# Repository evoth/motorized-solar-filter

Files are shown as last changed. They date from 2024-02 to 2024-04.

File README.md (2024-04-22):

# Motorized Solar Filter

A 3D printed solar filter that uses an SG90 servo to remove the solar film from your camera during totality!

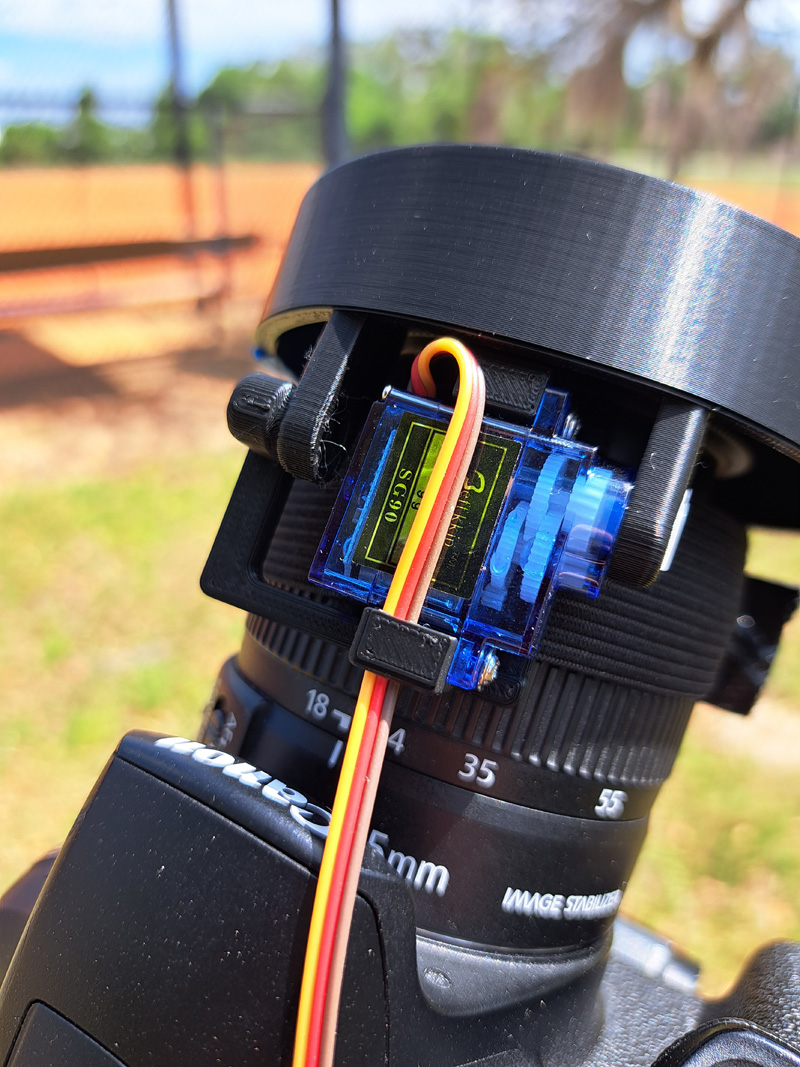
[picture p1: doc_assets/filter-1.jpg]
[](/doc_assets/filter-1_full.jpg)
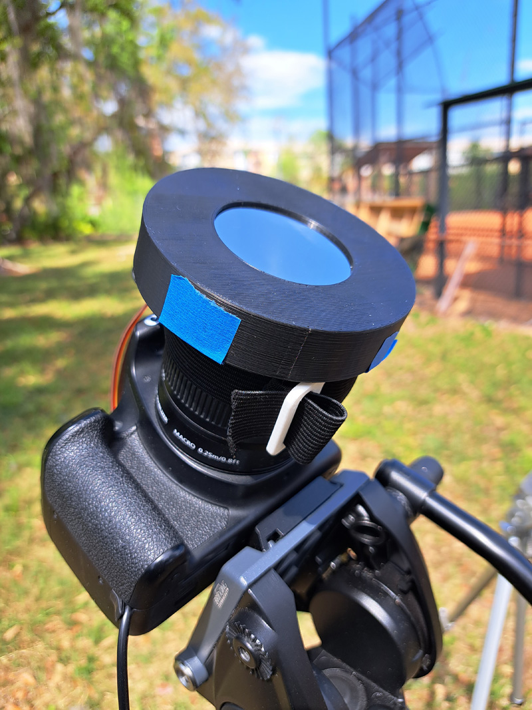
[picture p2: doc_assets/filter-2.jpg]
[](/doc_assets/filter-2_full.jpg)
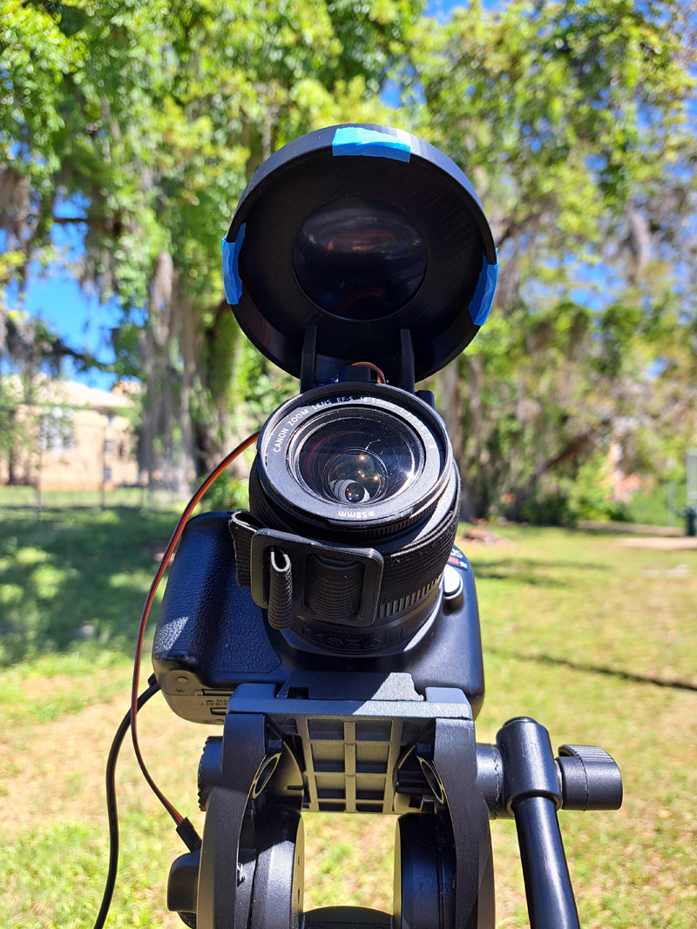
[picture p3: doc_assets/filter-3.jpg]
[](/doc_assets/filter-3_full.jpg)
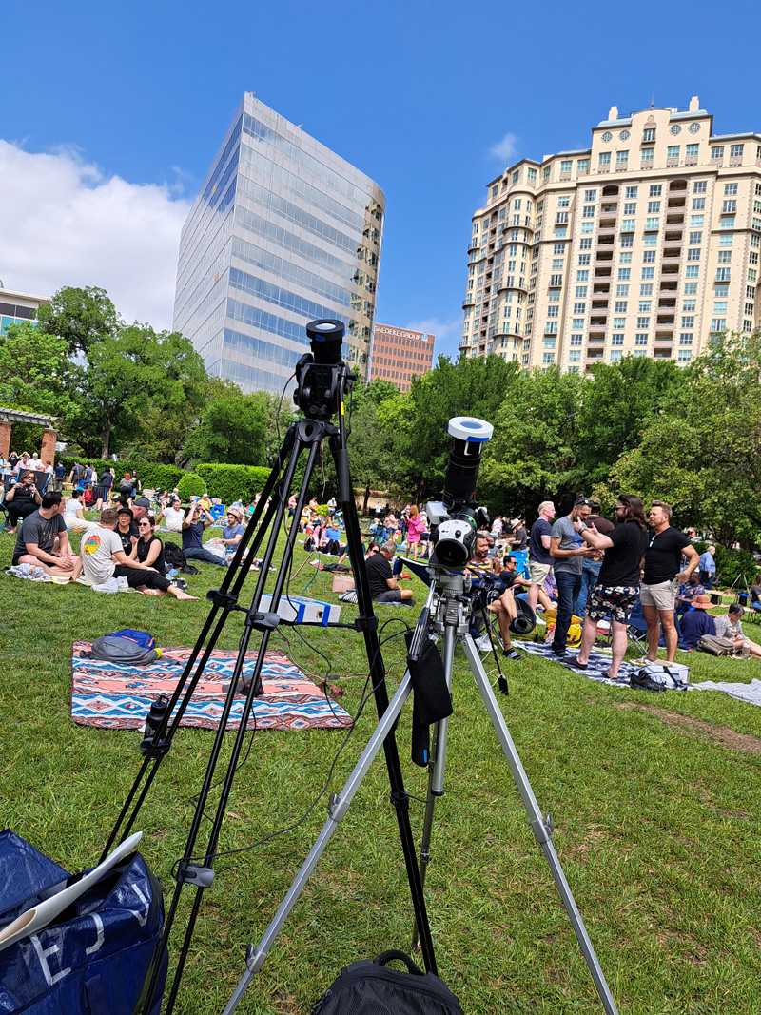
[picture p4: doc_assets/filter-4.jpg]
[](/doc_assets/filter-4_full.jpg)

## Materials

- 1 x [Filter inner piece](/stl/filter-inner.stl)
- 1 x [Filter outer piece](/stl/filter-outer.stl)
- 1 x [Servo holder](/stl/servo-holder.stl)
- 1 x [Tri-glide](/stl/tri-glide.stl) (quad-glide?)
- ~35cm long piece of 25mm width grippy/non-stick elastic band/strap (I used [this one from AliExpress](https://www.aliexpress.us/item/3256804311416876.html))
- Sheet of solar film at least 3x3 inches in size (I used this [Thousand Oaks film](https://www.amazon.com/Solar-Filter-Telescopes-Binoculars-Cameras/dp/B01770FDAC/))
- 1 x SG90 servo motor with attachment screws and ~21mm long servo arm/horn (I've tested [these](https://www.aliexpress.us/item/3256805486647239.html) and [these](https://www.amazon.com/dp/B07MLR1498))

## Instructions

Coming soon!

*Note: this filter was designed for 58mm outer diameter lenses (i.e. ø58mm). Because of the design's flexibility, it may work for smaller or similarly-sized lenses, but I haven't been able to confirm this myself.*

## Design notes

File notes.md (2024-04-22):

## Version 1

**Functionality:**
- Filter (outer):
    - Satisfactory.
- Filter (inner):
    - Does not fit servo arm (recess is too narrow and short).
- Servo holder:
    - Screws were too hard to turn.
    - Servo is not securely mounted.
- Tri-glide:
    - Satisfactory.

**Recommendations:**
- Filter (outer):
    - Wall thickness can be decreased to reduce weight.
- Filter (inner):
    - Wall thickness can be decreased to reduce weight. 
    - Redesign servo arm recess to fit measured dimensions of hardware.
- Servo holder:
    - Make the supports thicker with a tighter clearance for the motor.
    - Enlarge the screw holes for easier installation.
    - Add a hook on the bottom support to hold the servo cable.

## Version 2

**Functionality:**
- Filter (inner):
    - Satisfactory
- Servo holder:
    - Satisfactory

**Recommendations:**
- Filter (inner):
    - Clearances can be tightened to reduce play.
    - Faces of support arms can be extruded further outwards to hold servo arm more securely.
- Servo holder:
    - Clearances can be tightened to reduce play.
    - Top support should be returned to its previous height (making it taller was an accident)

## Version 3

**Functionality:**
- Filter (outer):
    - Satisfactory
- Filter (inner):
    - Satisfactory
- Servo holder:
    - Satisfactory

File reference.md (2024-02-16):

- [Swap-able Servo Mount](https://www.thingiverse.com/thing:2988830) by [Moarmau5](https://www.thingiverse.com/Moarmau5) on [Thingiverse](https://www.thingiverse.com/)
- [Tri-Glide Webbing Slide](https://www.printables.com/en/model/305674-tri-glide-webbing-slide-threaded-and-no-thread) by [Adam](https://www.printables.com/@Adam) on [Printables.com](https://www.printables.com/)
- [SG90 9g Micro Servo](https://www.autodesk.com/community/gallery/project/132949/sg90-9g-micro-servo) by [ccirone2](https://www.autodesk.com/community/gallery/profile/com-000093422339) on [Autodesk Community Gallery](https://www.autodesk.com/community/gallery)

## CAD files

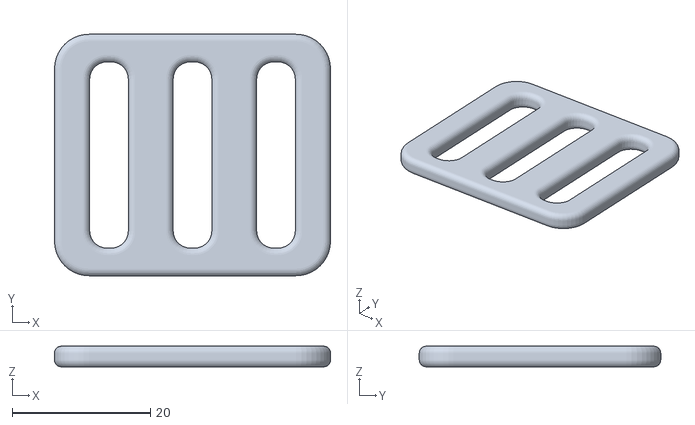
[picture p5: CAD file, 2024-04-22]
stl/tri-glide.stl
40.0 x 35.0 x 3.00

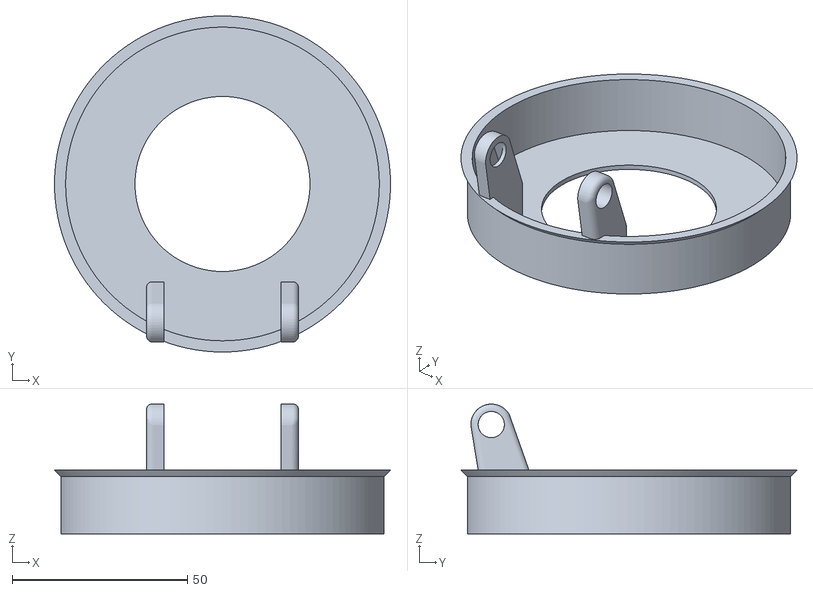
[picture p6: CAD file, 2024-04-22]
stl/filter-inner.stl
96.0 x 96.0 x 37.1

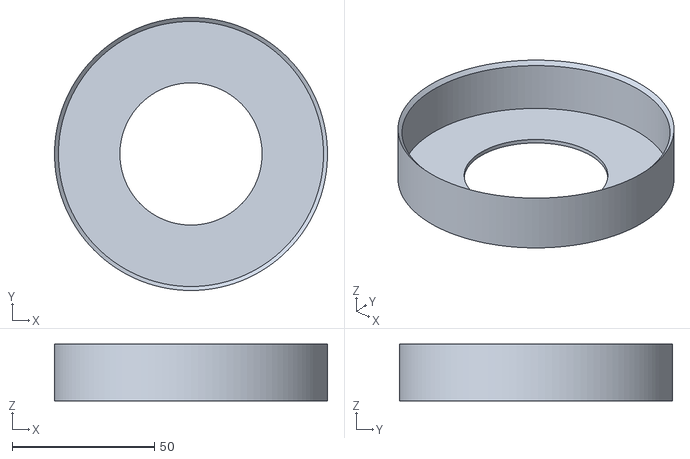
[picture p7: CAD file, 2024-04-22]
stl/filter-outer.stl
96.0 x 96.0 x 20.0

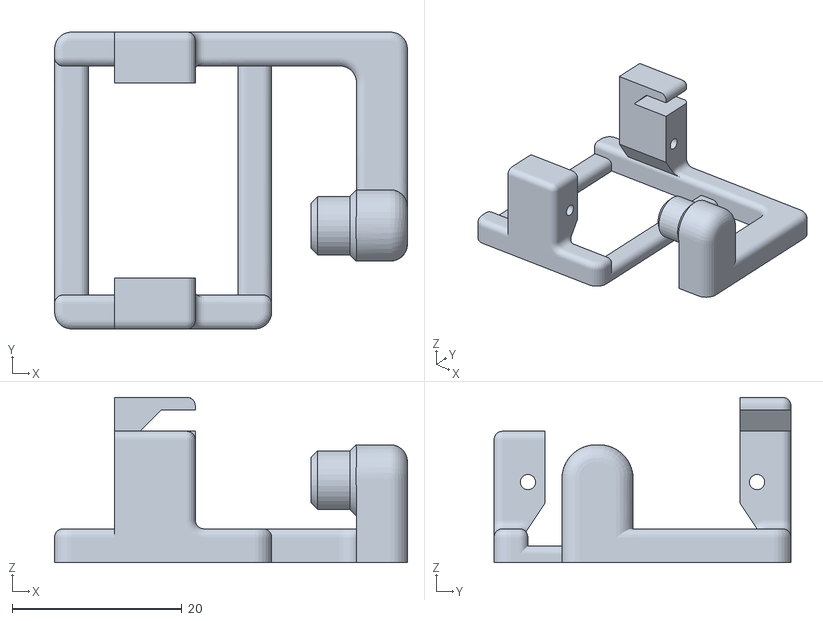
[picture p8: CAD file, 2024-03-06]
stl/servo-holder.stl
41.6 x 35.0 x 19.5

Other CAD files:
cad/Filter v25.f3z
cad/Filter v33.f3z
cad/Filter v35.f3z
cad/Filter v36.f3z
cad/ServoHolder v45.f3z
cad/ServoHolder v55.f3z
cad/ServoHolder v60.f3z
cad/TriGlide v3.f3d

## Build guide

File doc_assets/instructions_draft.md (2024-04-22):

Steps:
1. **3D print the four parts.**
    - The settings shouldn't matter too much, but make sure there isn't excessive support material that will be difficult to remove (the servo holder is usually the biggest culprit). Since I used a service at my college to print them, I'm not sure which settings they used, but I think it was around 0.2mm layer height and 15% infill.
2. **Cut a circle of circle film about 70-80mm in diameter.**
    - I used a roll of blue tape as a stencil, but as long as it can fit inside the outer filter piece without moving around too much, it should be fine.
3. **Place the solar film in the filter outer piece.**
    - The side that's supposed to face the sun (usually the shinier side if there is one) should face towards the base, away from the walls of the filter.
4. **Place the filter inner piece within the outer piece.**
    - They should fit snugly together and sandwich the film, leaving only a thin gap.
    - *Note: Make 100% sure there's no way that light can get through, even if you shake the filter. It's your responsibility to keep you and your equipment safe!*
5. **Fix the inner and outer pieces together.**
    - I used blue tape, but glue would also work. However, I recommend using a non-permanent method in case the solar film gets damaged and you need to replace it.
6. **Attach the servo to the servo holder.**
    - Use the included screws to screw it in.
    - The side with the gear must be on the side with the shorter post so that it's in line with the cylindrical piece on the other side!
7. **Attach the filter to the servo.**
    - Slide the filter into 
7. **Cut a piece of elastic strap about 35cm long (can always cut it shorter later).**

## Todo
- Add pictures to instructions and add more details

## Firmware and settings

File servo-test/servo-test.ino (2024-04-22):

#include <ServoEasing.hpp> 
ServoEasing servo;

int SERVO_PIN = 4;
int startpoint = 100;
int endpoint = 180;
int speed = 60;

void setup() {
  servo.attach(SERVO_PIN, endpoint, 544, 2400);
  servo.setEasingType(EASE_CUBIC_IN_OUT);
}

void loop() {
  pinMode(SERVO_PIN, INPUT);
  delay(5000);
  pinMode(SERVO_PIN, OUTPUT);
  servo.easeTo(startpoint, speed);
  pinMode(SERVO_PIN, INPUT);
  delay(5000);
  pinMode(SERVO_PIN, OUTPUT);
  servo.easeTo(endpoint, speed);
}

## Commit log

2024-02-16 First attempt; we'll see how it works!
    [Filter v25.f3z, ServoHolder v45.f3z, TriGlide v3.f3d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]
2024-02-28 Multiple adjustments, mainly to fit the servo arm
    [Filter v33.f3z, ServoHolder v55.f3z, Voth-Ethan-MSFM5.stl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]
2024-03-06 Fine tuning the fit and clearances
    [Filter v35.f3z, ServoHolder v60.f3z, Voth-Ethan-MSFM7.stl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]
2024-04-22 Basic docs (still need to add build instructions)
    [Filter v36.f3z, Voth-Ethan-MSFM1.stl, Voth-Ethan-MSFM2.stl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]
